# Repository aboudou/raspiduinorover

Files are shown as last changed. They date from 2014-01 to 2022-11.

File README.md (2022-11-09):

RaspiDuinoRover
===============

RaspiDuinoRover is a project about making a rover with a Raspberry Pi (and its camera module) and an Arduino Uno, and controlling it with an iPhone.

* [Youtube video of work in progress](http://www.youtube.com/watch?v=DCWTQt_jFEk)
* [Youtube video with tracked chassis](http://www.youtube.com/watch?v=M8OIg37Q50M)

Architecture
------------

RaspiDuinoRover is made of three main parts :

* A Raspberry Pi which receives commands from a remote device through a TCP connection, and sends these commands to an Arduino Uno through an I2C connection. The same TCP channel is used to send back to the remote data grabbed from the Arduino Uno about pan and tilt servo positions, camera lighting status and motors current usage. The Raspberry Pi also provides an MJPEG video stream from its camera module. 
* An Arduino Uno which receives commands from the Raspberry Pi though an I2C connection, and accordingly drives rover motors (with the help of an Arduino Motor Shield) and positions pan and tilt servos. It regularly gets infos about pan and tilt servo positions, camera lighting status and motors current usage, and send it back to the Raspberry Pi when asked for.
* An iOS device which serves as a remote control for the rover. It connects to the Raspberry Pi through a TCP connection, and displays its MJPEG video stream.

<p align="center">
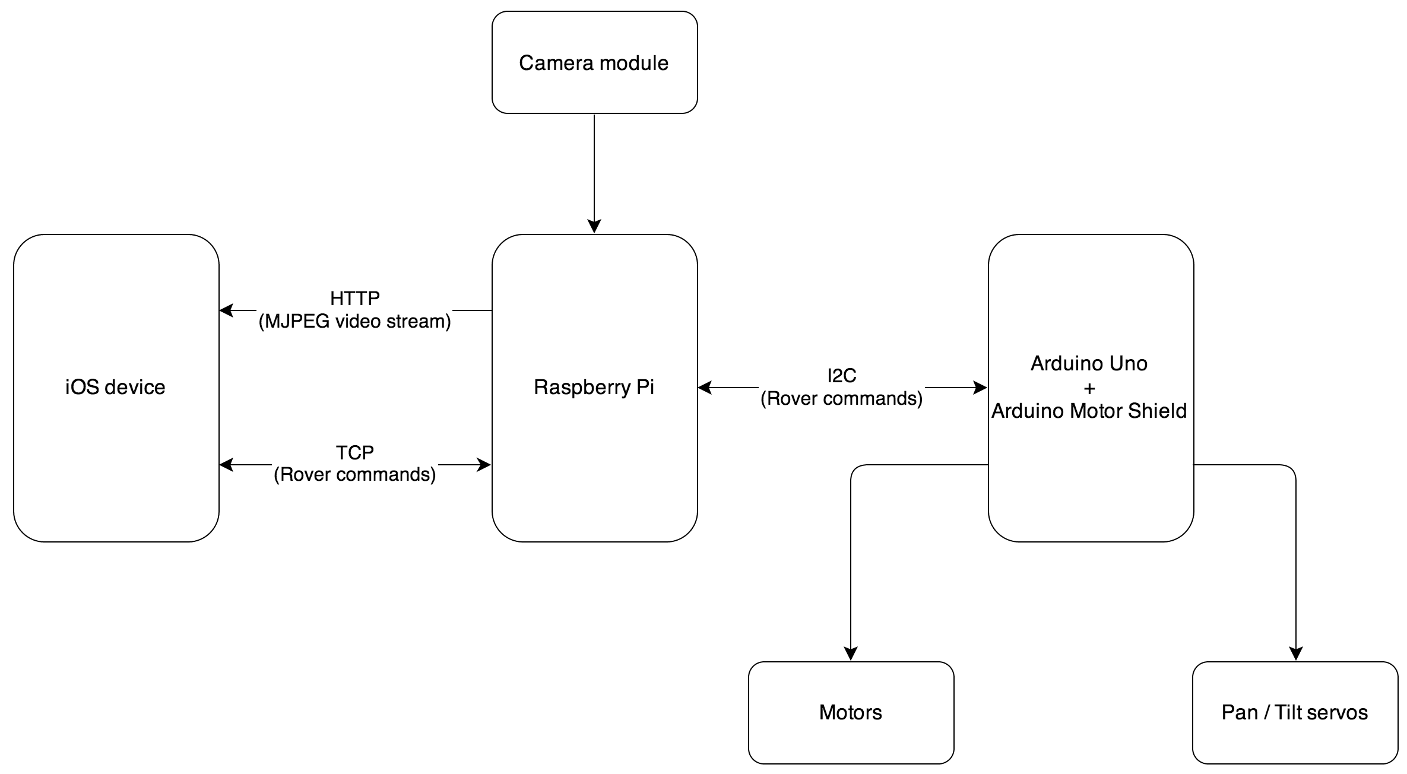
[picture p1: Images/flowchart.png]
Wiring diagram
  
  <br/>
  <em>Wiring diagram</em>
</p>

The base of the rover is made of a [Dagu Rover 5 Tracked Chassis](http://www.pololu.com/product/1550). The Raspberry Pi camera module is mounted on a pan/tilt support with servos, and a lighting feature based on three white LED is added to allow the use of the camera in the dark. It should be possible to replace camera module by a NoIR camera module and white LED with IR LED if you want / need a discreet illumination.

Servo motors, Raspberry Pi, Arduino Uno and camera lighting are powered by a common 5V power line. This 5V power may come from a wall power supply (at least 2A), while the chassis motors have their own power source. It may be possible to make a common power supply for all items, including chassis motors, but this page won't cover this topic.

Requirements
------------

* A Raspberry Pi.
* A Raspberry Pi camera module.
* An Arduno Uno R3.
* An Arduino Motor Shield R3.
* Some items listed into “bill_of_materials.ods” file.
* For server part :
	* Python (with Debian / Raspbian : packages “python”, “python-dev”).
	* SMBus library . On Raspbian, install package “python-smbus”.
	* Twisted library. On Raspbian, install package “python-twisted”.
	* UV4L (see below)
* For iPhone part :
	* An iPhone (or iPad, or iPod Touch) with iOS 7
	* XCode 5.0.x

To help you with the assembly, you may refer to the following files :

* RaspiDuinoRover.fzz: the global assembly, to open with Fritzing
  ([http://fritzing.org/](http://fritzing.org/)).
* CameraLighting.fzz: details for the camera support and lighting assembly, to open with Fritzing.
* PowerRail.fzz: details for the commond power rails.

Breadboard assembly and schematics
----------------------------------

<p align="center">
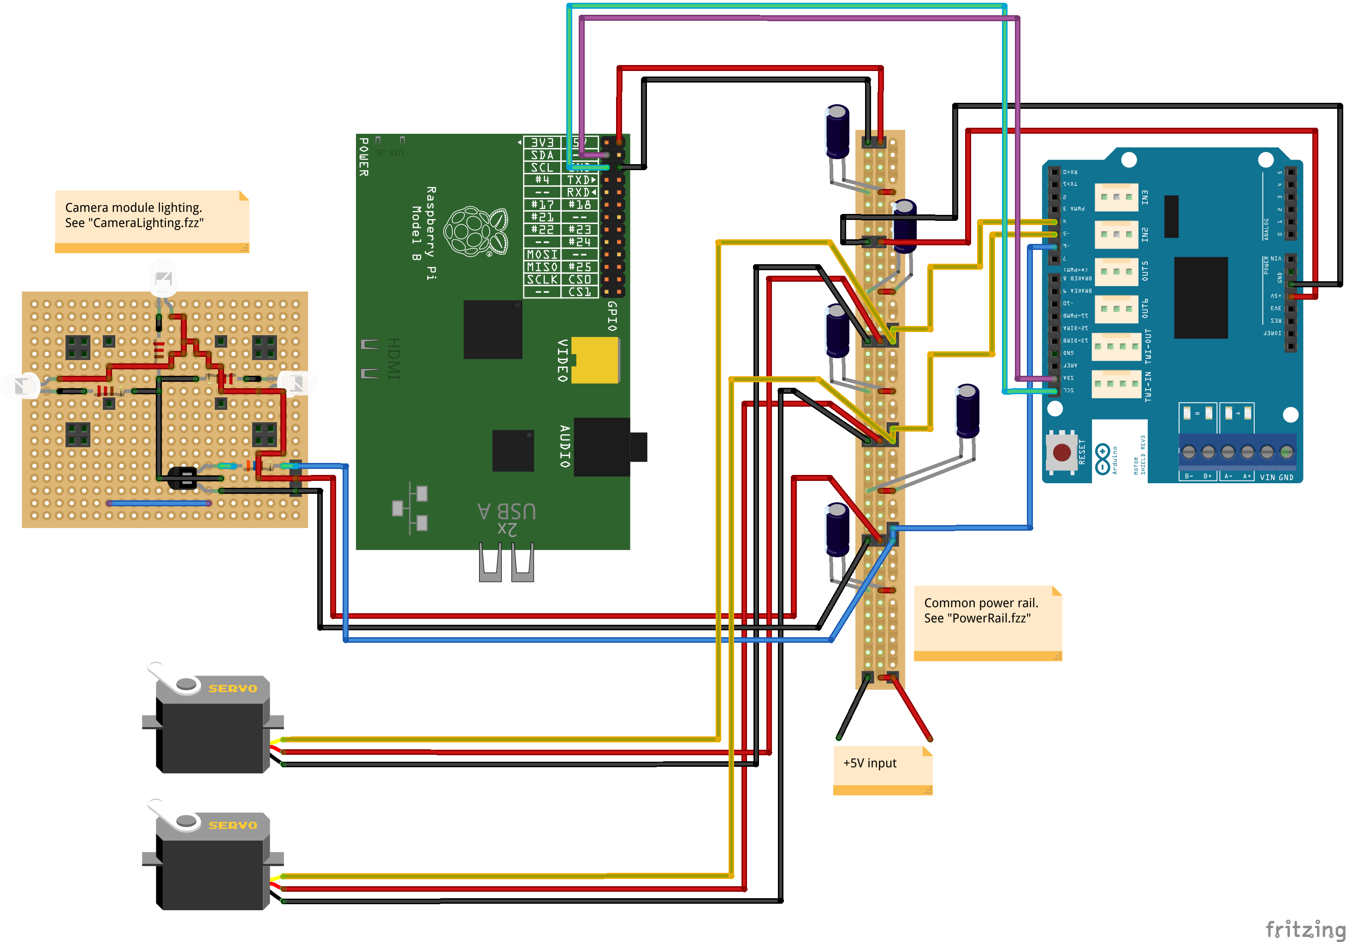
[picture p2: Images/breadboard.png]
Breadboard assembly
  
  <br/>
  <em>Breadboard assembly</em>

  <br/><br/>

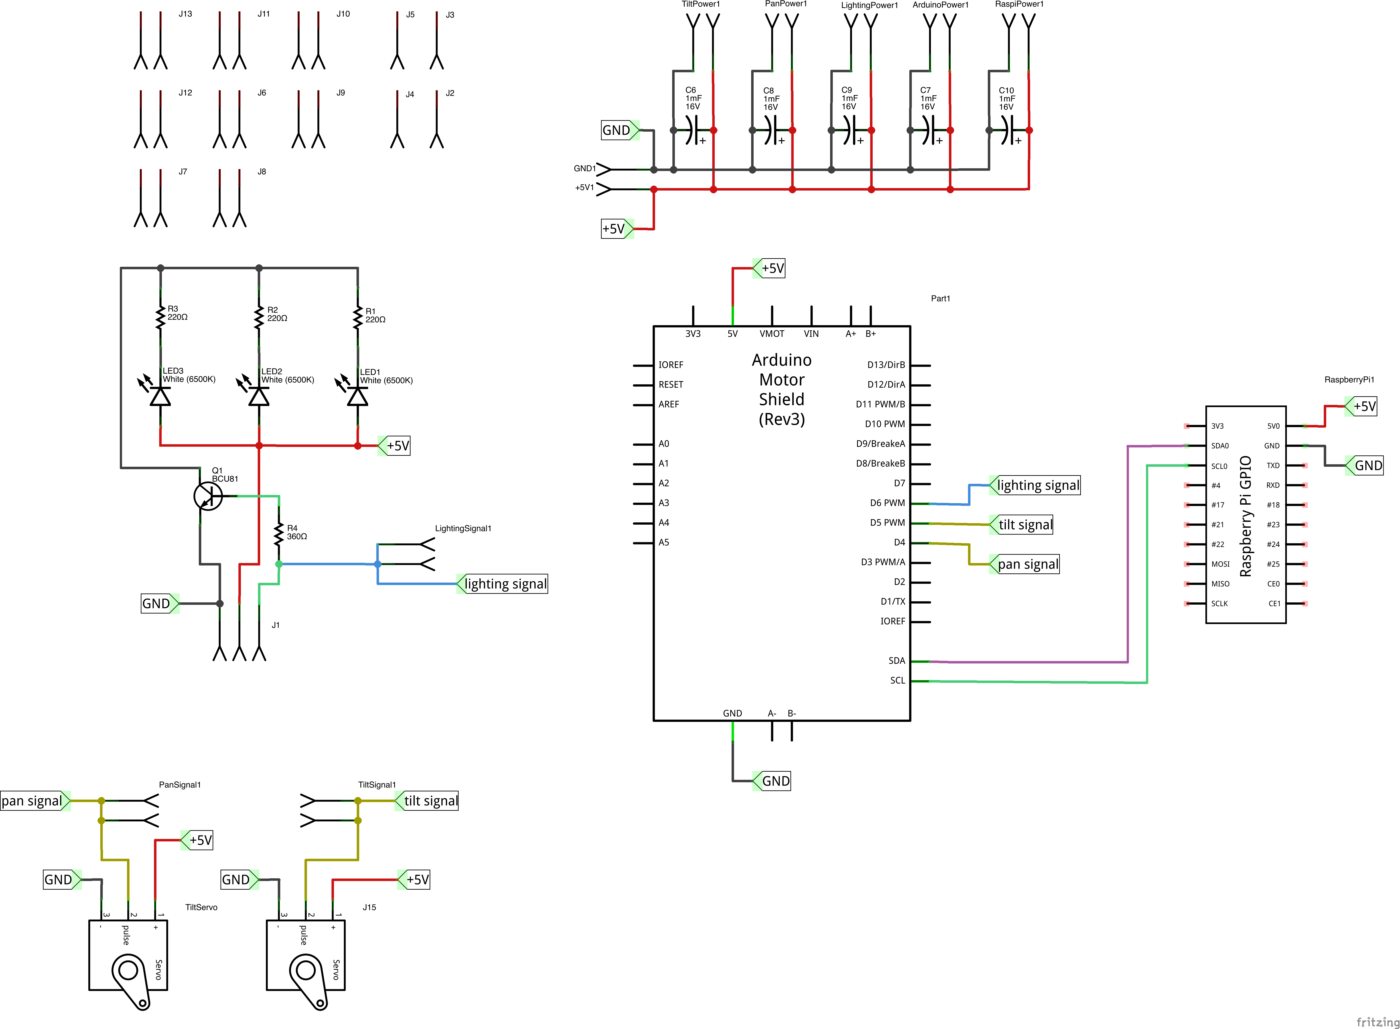
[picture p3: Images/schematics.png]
  
  <br/>
  <em>Schematics</em>
</p>

How to use RaspiDuinoRover (server)
-----------------------------------

You'll first have to upload “Arduino/Arduino.uno” sketch to your Ardunio Uno then build the assembly.

__Important:__ Don't forget to cut “Vin” jumper on the backside of the shield.

Then you have to install UV4L, following [these steps](https://www.linux-projects.org/uv4l/installation/). You'll need to install the following packages: “uv4l”, “uv4l-raspicam”, “uv4l-raspicam-extras” and “uv4l-server”.

You may want to use the following settings in “/etc/uv4l/uv4l-raspicam.conf” file (adapt to fit your needs):

```
width = 640
height = 360
framerate = 30
quality = 10
server-option = --port=8080
server-option = --use-ssl=no
```

then restart “uv4l_raspicam” service with “service uv4l_raspicam restart”.

Then update “./RaspberryPi/config.py” file to fit your needs.

When you're done, just launch RaspiDuinoRover with `./RaspberryPi/raspiduinorover.sh start` as root user. When you want / need to stop it, just execute `./RaspberryPi/raspiduinorover.sh stop` as root user.

The start script will start RaspiDuinoRover server.

Streaming will be started when a user connects to the server (have a look to ”./RaspberryPi/bin/stream.sh” script) and will be stopped when the last user disconnects.

How to use RaspiDuinoRemote (iPhone)
-----------------------------------------

Just open XCode project then build and install RaspiDuinoRemote on your iDevice. If you don't have an Apple iOS Developper account, you may use RaspiDuinoRemote within iOS Simulator.

When application is started, enter hostname (or IP adress) of your Raspberry Pi, the server port (default value is 8000, unless changed into “config.py” file) and MJPEG stream URL (it should be “http://&lt;raspberrypi_ip&gt;:8080/stream/video.mjpeg”. Then tap “Connect” button.

Some photos of the assembly
---------------------------

<p align="center">
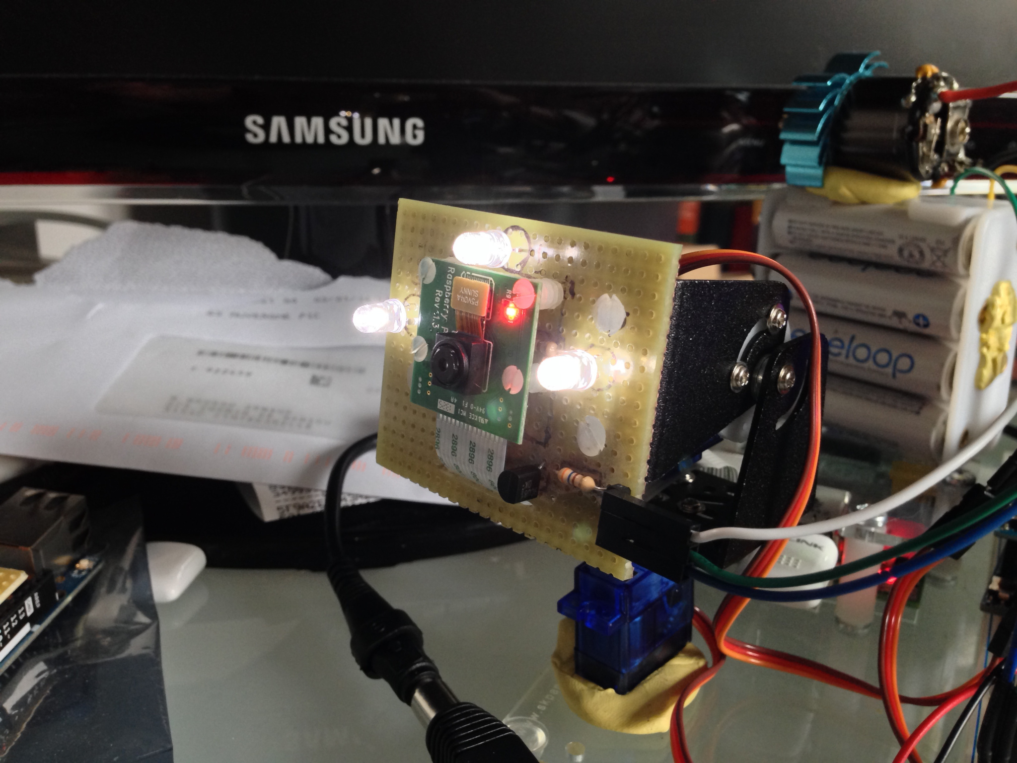
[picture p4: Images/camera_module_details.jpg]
Camera module lighting details
  
  <br/>
  <em>Camera module lighting details</em>

  <br/><br/>

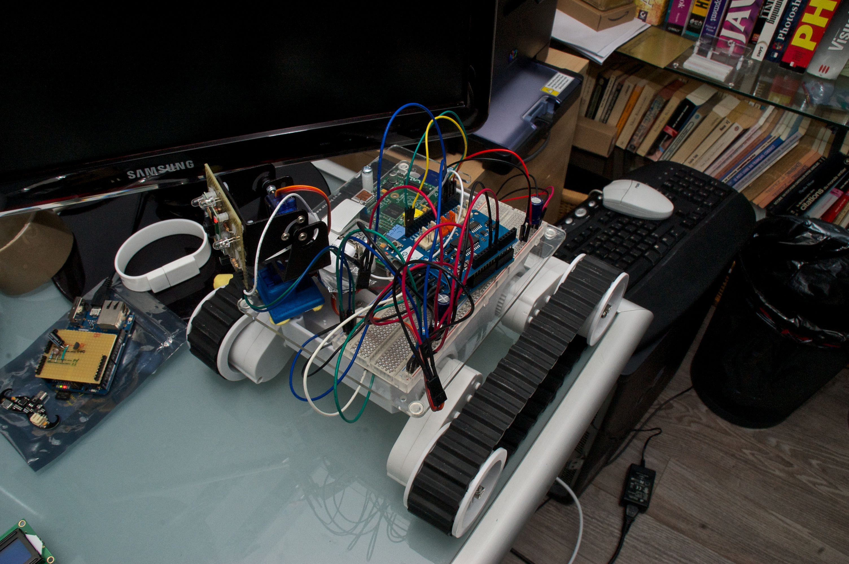
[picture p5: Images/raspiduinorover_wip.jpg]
Work in progress
  
  <br/>
  <em>Work in progress</em>

  <br/><br/>

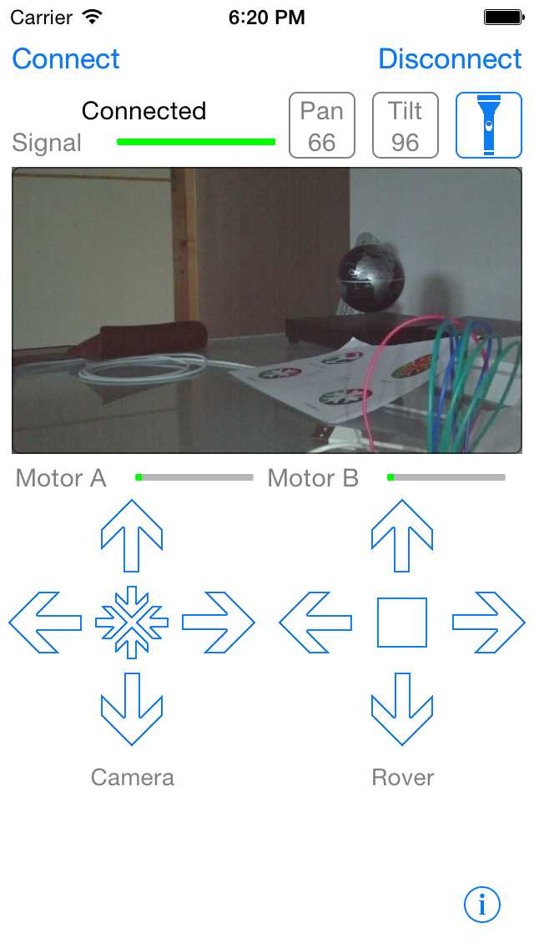
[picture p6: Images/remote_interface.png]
iOS remote
  
  <br/>
  <em>iOS remote, with motor current usage</em>
  
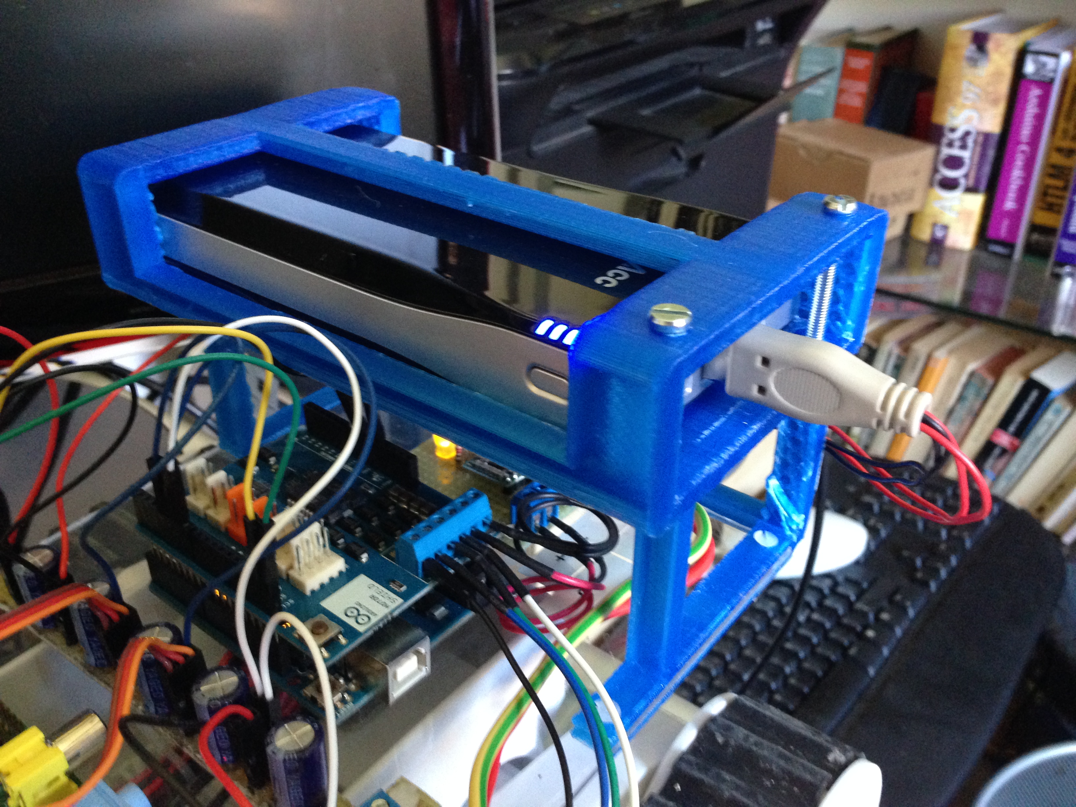
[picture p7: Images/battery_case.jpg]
Optional 3D printed battery case
  
  <br/>
  <em>Optional 3D printed battery case</em>

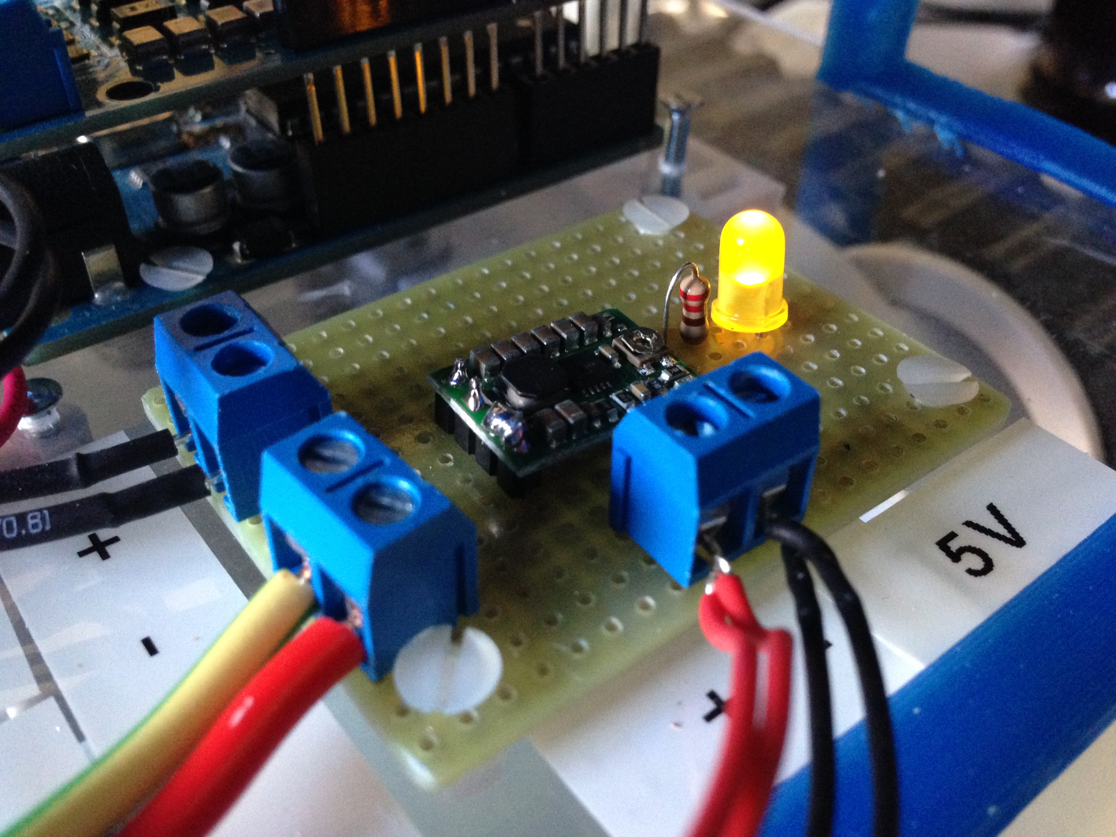
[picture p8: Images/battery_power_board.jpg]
Optional battery power board
  
  <br/>
  <em>Optional battery power board, used to provide +5V to common power rail and +8V to motor shield</em>
  
</p>

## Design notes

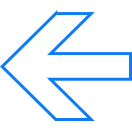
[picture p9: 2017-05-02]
iOS/RaspiDuinoRemote/RaspiDuinoRemote/move_left@3x.png

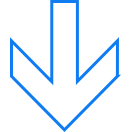
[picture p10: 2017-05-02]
iOS/RaspiDuinoRemote/RaspiDuinoRemote/move_backward@3x.png

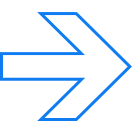
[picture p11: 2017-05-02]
iOS/RaspiDuinoRemote/RaspiDuinoRemote/move_right@3x.png

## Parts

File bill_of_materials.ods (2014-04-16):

Name | Part number | Online shop | Unit price | Number | Total price | Remarks
Raspberry Pi B | 7568308 | http://www.rs-particuliers.com/ | 32.88 | 1
Raspberry Pi Camera Module | 7757731 | http://www.rs-particuliers.com/ | 24.43 | 1
Arduino Uno R3 | 7697409 | http://www.rs-particuliers.com/ | 27.49 | 1
Arduino Motor Shield R3 | 7589349 | http://www.rs-particuliers.com/ | 28.8 | 1
Nylon M2x10mm bolt | 291290 | http://www.rs-particuliers.com/ | 7.33 | 11 |  | bag of 100 items
Nylon M2 nut | 528126 | http://www.rs-particuliers.com/ | 7 | 22 |  | bag of 50 items
Nylon M3x10mm bolt | 291363 | http://www.rs-particuliers.com/ | 7.16 | 10 |  | bag of 100 items
Nylon M3 nut | 525701 | http://www.rs-particuliers.com/ | 12.36 | 22 |  | bag of 50 items
White LED | 7133992 | http://www.rs-particuliers.com/ | 0.9 | 3
360 ohm resistor, 0.25W, 5% | 7077631 | http://www.rs-particuliers.com/ | 0.02 | 1
220 ohm resistor, 0.25W, 5% | 7077612 | http://www.rs-particuliers.com/ | 0.02 | 3
BCU81 transistor | 7387553 | http://www.rs-particuliers.com/ | 0.4 | 1
1000µF electrolytic capacitor | 7152577 | http://www.rs-particuliers.com/ | 0.53 | 5
Pan & Tilt servo support | 25925 | http://www.gotronic.fr/ | 13.7 | 1
Rover 5 Robot Platform | POL-01550 | http://snootlab.com/ | 59.7 | 1
Optional
12000 mAh power bank | PB12000A | http://www.amazon.fr/ | 37.99 | 1
Adjustable voltage regulator | S7V8A | http://snootlab.com/ | 6.5 | 1
other userful stuff: - male header strip - angled male header strip - male to female jumper wires - male to male jumper wires - stripboard - perfboard

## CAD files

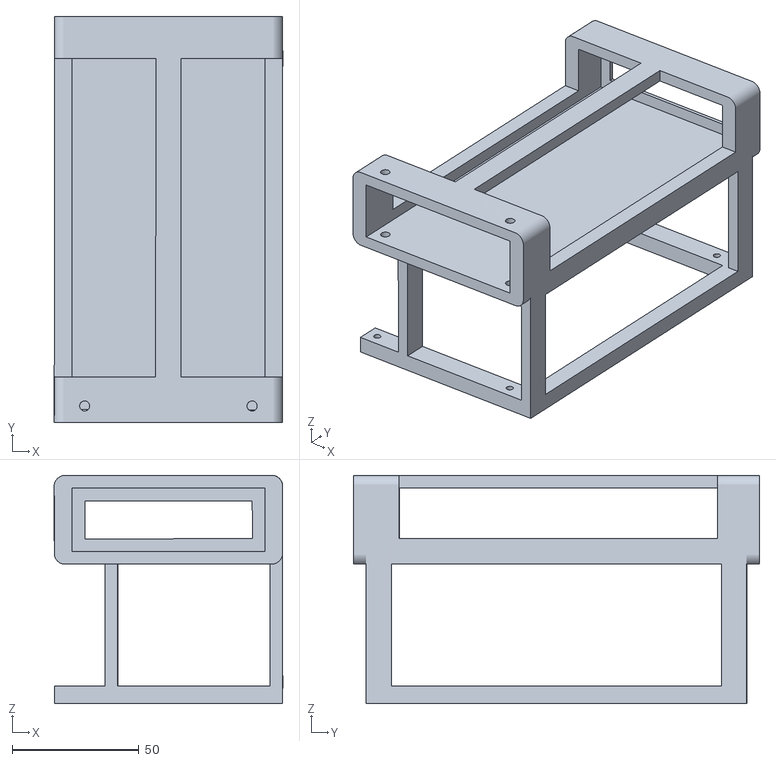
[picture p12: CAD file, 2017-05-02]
Optional/battery_case.stl
90.1 x 160.0 x 90.0

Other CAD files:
Optional/battery_case.skp

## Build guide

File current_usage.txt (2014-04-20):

Raspberry Pi model B
 - TL-WN723N USB Wireless adapter
 - Raspberry Pi camera module
 - No keyboard, no HMDI / composite display
 - No overclock
 - Arduino UNO through I2C connection

Arduino UNO + Arduino Motor Shield

In this case, motors of tracked chassis are powered by the common power rail.

Current usage was measured at the input of the common power rail, thus measuring current usage of
 - Raspberry Pi
 - Arduino Uno
 - Arduino Motor Shield
 - Pan / Tilt servos
 - Lighting module
 - Tracked chassis motors

Idle mode is when nobody is connected to the rover:
 - Raspberry Pi does not communicate with Arduino UNO
 - Raspberry Pi camera module is stopped
 - Tracked chassis motors are stopped
 - Pan / Tilt servos are detached from Arduino (a.k.a. no signal on control pins)
 - Lighting module is switched off

Active mode is when someone is connected to the rover:
 - Raspberry Pi regularly get status from Arduino UNO (every 0.5 seconds)
 - Raspberry Pi camera module is running, with active streaming
 - Tracked chassis motors may be running
 - Pan / Tilt servos are attached to Arduino (a.k.a. signal on control pins), and may be moving
 - Lighting module may be switched on

Results:

idle mode  : 460 mA

active mode: 730 mA streaming (user just connected, no action)
             750 mA streaming + lights on
             750 mA streaming + servo moving
             800 mA streaming + servo moving + lights on
             1750 mA streaming + motors running
             1800 mA streaming + motors running + lights on

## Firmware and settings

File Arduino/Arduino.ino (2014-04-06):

#include <Wire.h>
#include <Servo.h>

// I2C message to keep Arduino alive
#define CMD_KEEP_ALIVE 1

// I2C message to switch light status (on/off)
#define CMD_LIGHT_SWITCH 10

// I2C message to move pan servo to left
#define CMD_SERVO_PAN_LEFT 20
// I2C message to move pan servo to right
#define CMD_SERVO_PAN_RIGHT 21
// I2C message to move tilt servo to up
#define CMD_SERVO_TILT_UP 22
// I2C message to move tilt servo to down
#define CMD_SERVO_TILT_DOWN 23
// I2C message to center servos
#define CMD_SERVO_CENTER 24

// I2C message to stop all moves
#define CMD_MOVE_STOP 30
// I2C message to move forward
#define CMD_MOVE_FORWARD 31
// I2C message to move backward
#define CMD_MOVE_BACKWARD 32
// I2C message to turn left
#define CMD_TURN_LEFT 33
// I2C message to turn right
#define CMD_TURN_RIGHT 34

// I2C message to handle connection to rover
//  - Light off
//  - Pan & tilt servos to 90 degrees
//  - Motors off
#define CMD_CONNECT 254
// I2C message to handle disconnection from rover
//  - Light off
//  - Detach servo motors
//  - Motors off
#define CMD_DISCONNECT 255

// Definition of useful pins
#define PIN_LIGHT 6
#define PIN_SERVO_PAN 4
#define PIN_SERVO_TILT 5
#define PIN_MOTOR_PWM_A 3
#define PIN_MOTOR_PWM_B 11
#define PIN_MOTOR_DIR_A 12
#define PIN_MOTOR_DIR_B 13
#define PIN_MOTOR_CURRENT_A A0
#define PIN_MOTOR_CURRENT_B A1

// Definition of min and max servos angles
// You might have to switch left/right and up/down values
//   depending on servos placement
#define MAX_LEFT_ANGLE 180
#define MAX_RIGHT_ANGLE 0
#define MAX_DOWN_ANGLE 120
#define MAX_UP_ANGLE 0

// Tilt and Pan servo steps value
#define TILT_SERVO_STEP 2;
#define PAN_SERVO_STEP 2;

// Servo objects
Servo servoPan;
Servo servoTilt;

// I2C communication variables (master to slave)
volatile byte cmd = 0;
volatile byte param = 0;

// I2C communication variables (slave to master)
volatile byte motorCurrentA;
volatile byte motorCurrentB;
volatile byte lightState;
volatile int panAngle;  // To understand use of int instead of byte, see below
volatile int tiltAngle; // To understand use of int instead of byte, see below

/*
 * I use int for servoAngle values because of the way I use constrain() to limit
 * servo angle values. The issue is when I decrease angle value, and minimum angle
 * values of 0.
 *
 * The behavior is the following:
 * - Decrease current angle by 1
 * - Constrain value between min and max angle values
 *
 * With byte values, and minimum angle value of 0, I got the following behavior:
 * currentAngle = 0
 * currentAngle - 1 = 255 (byte range is from 0 to 255, no negative values possible)
 * after constrain: currentAngle = maxAngle value
 * You will see the servo jump from its min angle position to its max angle position.
 *
 * With int values, and minimum angle value of 0, I got the following behavior:
 * currentAngle = 0
 * currentAngle - 1 = -1 (int range is from -32,768 to 32,767)
 * after constrain: currentAngle = 0
 * The servo will stay at its current position.
 */

void setup() {
  // Start as I2C slave device, with adress 0x42 (we don't know the question yet)
  Wire.begin(0x42);

  // Register callback for received events
  Wire.onReceive(receiveEvent);
  Wire.onRequest(requestEvent);

  // Disable internal pull-ups on I2C pins  
  #ifndef cbi
  #define cbi(sfr, bit) (_SFR_BYTE(sfr) &= ~_BV(bit))
  #endif
  #if defined(__AVR_ATmega168__) || defined(__AVR_ATmega8__) || defined(__AVR_ATmega328P__)
    // deactivate internal pull-ups for twi
    // as per note from atmega8 manual pg167
    cbi(PORTC, 4);
    cbi(PORTC, 5);
  #else
    // deactivate internal pull-ups for twi
    // as per note from atmega128 manual pg204
    cbi(PORTD, 0);
    cbi(PORTD, 1);
  #endif
  
  // Init pin modes and servo objects
  pinMode(PIN_LIGHT, OUTPUT);

  pinMode(PIN_MOTOR_PWM_A, OUTPUT);
  pinMode(PIN_MOTOR_PWM_B, OUTPUT);

  pinMode(PIN_MOTOR_DIR_A, OUTPUT);
  pinMode(PIN_MOTOR_DIR_B, OUTPUT);
  
  // Switch to default state
  roverDisconnect();
}

void loop() {
  // Execute received commands
  if (cmd != 0) {
    switch (cmd) {
      case CMD_KEEP_ALIVE:
        // Do nothing
        break;
      
      case CMD_LIGHT_SWITCH:
        switchLight();
        break;
      
      case CMD_MOVE_STOP:
        moveStop();
        break;
  
      case CMD_MOVE_FORWARD:
        moveForward();
        break;
  
      case CMD_MOVE_BACKWARD:
        moveBackward();
        break;
  
      case CMD_TURN_LEFT:
        turnLeft();
        break;
  
      case CMD_TURN_RIGHT:
        turnRight();
        break;
  
      case CMD_DISCONNECT:
        roverDisconnect();
        break;
  
      case CMD_CONNECT:
        roverConnect();
        break;
  
      case CMD_SERVO_PAN_LEFT:
        moveServoPanLeft();
        break;
  
      case CMD_SERVO_PAN_RIGHT:
        moveServoPanRight();
        break;

      case CMD_SERVO_TILT_UP:
        moveServoTiltUp();
        break;
  
      case CMD_SERVO_TILT_DOWN:
        moveServoTiltDown();
        break;

      case CMD_SERVO_CENTER:
        moveServoCenter();
        break;

    }
    // Reset command
    cmd = 0;
  }
  
  // Get light and motor statuses
  lightState = (byte)(digitalRead(PIN_LIGHT));
  motorCurrentA = (byte)map(analogRead(PIN_MOTOR_CURRENT_A), 0, 1023, 0, 255);
  motorCurrentB = (byte)map(analogRead(PIN_MOTOR_CURRENT_B), 0, 1023, 0, 255);

}

// Callback function for I2C events
void receiveEvent(int msgSize) {
  if (msgSize == 1) {
    // Case of one byte message
    cmd = Wire.read();
          
  } else if (msgSize == 2) {
    // Case of two bytes message
    //   - First byte is the command
    //   - Second byte is the parameter       
    cmd = Wire.read();
    param = Wire.read();

  } else {
    while (Wire.available() > 0) {
      // Flush message buffer
      Wire.read();
    }
  }
}

// Callback function for I2C requests
void requestEvent() {
  byte data[] = {lightState, motorCurrentA, motorCurrentB, panAngle, tiltAngle};
  Wire.write(data, 5);
}

// Switch light status
void switchLight() {
  digitalWrite(PIN_LIGHT, !(digitalRead(PIN_LIGHT)));
}

// Move pan servo left
void moveServoPanLeft() {
  if (MAX_RIGHT_ANGLE > MAX_LEFT_ANGLE) {
    panAngle -= PAN_SERVO_STEP;
    panAngle = constrain(panAngle, MAX_LEFT_ANGLE, MAX_RIGHT_ANGLE);
  } else { 
    panAngle += PAN_SERVO_STEP
    panAngle = constrain(panAngle, MAX_RIGHT_ANGLE, MAX_LEFT_ANGLE);
  }
  servoPan.write(panAngle);
}

// Move pan servo right
void moveServoPanRight() {
  // Depending on servo placement, you may have to use panAngle++ instead
  if (MAX_RIGHT_ANGLE > MAX_LEFT_ANGLE) {
    panAngle += PAN_SERVO_STEP;
    panAngle = constrain(panAngle, MAX_LEFT_ANGLE, MAX_RIGHT_ANGLE);
  } else { 
    panAngle -= PAN_SERVO_STEP;
    panAngle = constrain(panAngle, MAX_RIGHT_ANGLE, MAX_LEFT_ANGLE);
  }
  servoPan.write(panAngle);
}

// Move tilt servo up
void moveServoTiltUp() {
  if (MAX_UP_ANGLE > MAX_DOWN_ANGLE) {
    tiltAngle += TILT_SERVO_STEP;
    tiltAngle = constrain(tiltAngle, MAX_DOWN_ANGLE, MAX_UP_ANGLE);
  } else {
    tiltAngle -= TILT_SERVO_STEP;
    tiltAngle = constrain(tiltAngle, MAX_UP_ANGLE, MAX_DOWN_ANGLE);
  }
  servoTilt.write(tiltAngle);
}

// Move tilt servo down
void moveServoTiltDown() {
  if (MAX_UP_ANGLE > MAX_DOWN_ANGLE) {
    tiltAngle -= TILT_SERVO_STEP;
    tiltAngle = constrain(tiltAngle, MAX_DOWN_ANGLE, MAX_UP_ANGLE);
  } else {
    tiltAngle += TILT_SERVO_STEP;
    tiltAngle = constrain(tiltAngle, MAX_UP_ANGLE, MAX_DOWN_ANGLE);
  }
  servoTilt.write(tiltAngle);
}

// Center servos
void moveServoCenter() {
  panAngle = 90;
  tiltAngle = 90;
  servoPan.write(panAngle);
  servoTilt.write(tiltAngle);
}

// Make rover stop moving
// We don't use brakes, just let them stop by themselves
void moveStop() {
  analogWrite(PIN_MOTOR_PWM_A, 0);
  analogWrite(PIN_MOTOR_PWM_B, 0);
}

// Make rover move forward
void moveForward() {
  digitalWrite(PIN_MOTOR_DIR_A, HIGH);
  digitalWrite(PIN_MOTOR_DIR_B, HIGH);
  
  analogWrite(PIN_MOTOR_PWM_A, 255);
  analogWrite(PIN_MOTOR_PWM_B, 255);
}

// Make rover move backward
void moveBackward() {
  digitalWrite(PIN_MOTOR_DIR_A, LOW);
  digitalWrite(PIN_MOTOR_DIR_B, LOW);
  
  analogWrite(PIN_MOTOR_PWM_A, 255);
  analogWrite(PIN_MOTOR_PWM_B, 255);
}

// Make rover turn left
void turnLeft() {
  digitalWrite(PIN_MOTOR_DIR_A, HIGH);
  digitalWrite(PIN_MOTOR_DIR_B, LOW);
  
  analogWrite(PIN_MOTOR_PWM_A, 255);
  analogWrite(PIN_MOTOR_PWM_B, 255);
}

// Make rover turn right
void turnRight() {
  digitalWrite(PIN_MOTOR_DIR_A, LOW);
  digitalWrite(PIN_MOTOR_DIR_B, HIGH);
  
  analogWrite(PIN_MOTOR_PWM_A, 255);
  analogWrite(PIN_MOTOR_PWM_B, 255);
}

// Make rover goes to default state
//  - Light switched off
//  - Motors stopped
//  - Servos centered
void roverDisconnect() {
  digitalWrite(PIN_LIGHT, LOW);
  moveStop();
  servoPan.detach();
  servoTilt.detach();
}

void roverConnect() {
  digitalWrite(PIN_LIGHT, LOW);
  moveStop();
  servoPan.attach(PIN_SERVO_PAN);
  servoTilt.attach(PIN_SERVO_TILT);
  moveServoCenter();
}
  

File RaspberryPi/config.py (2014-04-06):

import os

"""
" Edit below this line to fit your needs
"""

# Interface to LISTEN ("0.0.0.0" for all interfaces)
IFACE = "0.0.0.0"

# Network port to LISTEN
PORT = 8000

# I2C bus to use : 0 for older Raspberry Pi model B 256MB, 1 for others
I2CBUS = 1

# I2C address of the slave Arduino
ADDRESS = 0x42

# Get path of config file
CONFIG_PATH = os.path.dirname(os.path.realpath(__file__))
# Streaming start script
STREAM_START = [CONFIG_PATH + "/bin/stream.sh", "start"]
# Streaming stop script
STREAM_STOP = [CONFIG_PATH + "/bin/stream.sh", "stop"]

# WLAN adapter (default "wlanO", empty if you don't want / need to get
#   signal strength).
WLAN_ADAPTER = "wlan0"

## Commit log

2014-01-14 Typo + clarification on flowchart
2014-01-15 README.md and Fritzing update
    [RaspiDuinoRover.fzz]
2014-02-08 Switch to Fritzing 0.8.7 file format
    [CameraLighting.fzz, PowerRail.fzz, RaspiDuinoRover.fzz]
2014-02-08 Some typos in Fritzing files
    [PowerRail.fzz, RaspiDuinoRover.fzz]
2014-02-08 Updated bill of materials
    [bill_of_materials.ods]
2014-02-09 Better behavior for servo movements
2014-02-09 Fix streaming start script config
    [config.py]
2014-02-12 Disconnection from rover nows detach servo motors to use less current when rover is idle
2014-02-12 When no client is connected, we release I2C connection to save CPU cycles and current usage
2014-02-12 Disconnection from rover nows detach servo motors to use less current when rover is idle (oops)
2014-02-12 Added current usage measurements
2014-02-12 Added info of power usage measurements
2014-02-12 Added more info of power usage measurements
2014-02-12 Fixed threading issues
2014-02-12 With tracked chassis video
2014-03-30 Added constants for servo steps values
2014-04-16 Added infos for optional Powerbank support
    [battery_case.skp, battery_case.stl, battery_power_board.fzz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]
2014-04-16 Explanation on battery power board
2014-04-20 Updated current usage
2014-07-29 Another iteration for battery case
    [battery_case.skp, battery_case.stl]
